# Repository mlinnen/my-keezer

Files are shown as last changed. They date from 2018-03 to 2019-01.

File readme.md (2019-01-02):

# Overview
This is my custom controller for my keezer.  I am building this from the ground up because I have some very specific ideas that I want to include and I have found no other solution (custom or off the self) that meets my needs.

## Build status
Master Branch  
Dev Branch 

## Goals 
I have a number of goals I want to achieve for this custom controller.  At this point I doubt all of this could or should be done on a single ESP8266 micro.  It is likely I will have a number of ESP8266's that work together over MQTT to achieve all of the functionality I want.  This project will evolve over a long period of time.

### Future list of features
Check out the [Github Issues (label enhancements)](https://github.com/mlinnen/my-keezer/labels/enhancement) for a list of features that are planned for a later date.

## Features
This is a list of actual features the current code base supports.

### Current list of features
* Measure the temperature inside the keezer with two temperature sensors (one at the top and one at the bottom).
* Measure the temperature outside the keezer.
* Control the keezer temperature given a temperature set point and the temperature sensor reading ().
* Display the current temperature of the keezer on an LCD.
* Turn on/off a fan(s) to circulate the air in the keezer when the difference between the top and bottom sensors is greater than a given threshold.  
* Detect motion when someone approaches the keezer.
* Turn on LED lighting and LCD display when someone approaches and turn off the lighting and LCD display after a delay.
* Connects to MQTT broker using a user name and password.
* Broadcast over MQTT sensor readings such as: temperature and motion.
* Broadcast over MQTT event changes such as: compressor, fan and lights turning on/off.
* Respond to an MQTT ping request so that an external application can determine what keezers are online.
* Allow the keezer to join a wifi network without changing the code
* Allow for the keezer to join a new Wifi or a different MQTT broker by holding down the mode pushbutton for > 3 seconds.
* The keezer continues to maintain the temperature of the beer even if the Wifi is down or the MQTT broker is down.  The highest priority is to keep the beer nice and cold.

## Hardware
* 3 DS18B20 Temperature Sensors
* 1 4.7K Resistor
* 1 [HUZZAH ESP8266](https://www.adafruit.com/product/2471)
* 1 [4 Channel Relay Board](https://www.sunfounder.com/4-channel-5v-relay-shield-module.html)
* 1 [4 x 20 LCD](https://www.adafruit.com/product/498)
* 1 [I2C / SPO character LCD backpack](https://www.adafruit.com/product/292)
* 1 [12v 5A switching power supply](https://www.adafruit.com/product/352)
* 1 [Mini DC/DC Converter 5v @ 1A](https://www.adafruit.com/product/1065)
* 1 [LED Strip Light Triangle Bulbs](https://www.amazon.com/Triangle-Bulbs-T93003-Waterproof-Flexible/dp/B00IZA2URS)

## Wiring
I used Fritzing to document the wiring of all components.  After installing Fritzing just open the doc\keezer.fzz file from Fritzing.  Or you can look at the doc\Wiring.png file.

## I/O
* 1 gpio for 1 wire for temperature sensors
* 1 gpio for relay dc fan
* 1 gpio for relay LED light strip
* 1 gpio for relay compressor
* 1 gpio for motion sensor
* 2 gpio for LCD
* 1 gpio for push button LCD mode

### LCD Display layout
A push button allows you to change the mode of the LCD.  Mode 1 is the default mode and after a certain amount of time the LCD will fall back into this mode.

Example Mode 1 Top, Average & Bottom Compressor on
```
Current Temperature
Set  43.0 Top 44.5
          Avg 43.5
Comp On   Bot 42.5
```  
Example Mode 1 Top, Average & Bottom Compressor off
```
Current Temperature
Set  43.0 Top 44.5
          Avg 43.5
Comp Off  Bot 42.5
```  

Example Mode 2 External Temperature
```
Current Temperature
          Ext 82.0
        
Comp Off          
```

Example Mode 3 Set Temperature
```
Set Temperature
High          44.0
Avg           43.0
Low           42.0
```

## Dependencies
This application depends on the following libraries:
* OneWire
* DallasTemperature
* RBD_Timer
* RBD_Button
* Adafruit LiquidCrystal
* PubSubClient
* WifiManager
* ArduinoJson

## Build
There are a couple things you need to do so that you can compile the project. I converted this project to use [Platform IO](https://platformio.org/) so you will need to install it as well as an editor. I personally think that the Visual Studio code editor works very well with Platform IO.

1. Make a copy of the myconfig.sample.h and rename it myconfig.h
2. Edit the myconfig.h and set the specific topics that you want the keezer to use (or leave them as is).  If you have more than 1 keezer make sure you changed the integer in all the topics so that one keezer can be addressed differently than the other keezer
3. You can also make changes to the default settings in myconfig.h
4. TODO Detail how someone sets the right index values for the temperature sensors since they are different for every sensor.
5. Place the ESP8266 into flash mode
6. Run the following command 
        pio run --target upload
7. The first time that the application is downloaded to the target platform it will put the device in an Access Point mode which will allow you to configure it for connection to your Wifi
8. Open your Wifi and connect to "mykeezer-ap". Note you have 120 seconds after power on to complete this task before the keezer falls out of AP mode and starts controlling the temperature of the beer.  If you dont complete this process before the 120 second timeout simply cycle the power on the keezer and try again
9. Click on the Wifi setup button and fill in the text fields.  Once the information is submitted the device will connect to Wifi and the MQTT broker
10. If you need to change the MQTT or Wifi settings just hold in the mode button for longer than 4 seconds and the device will become an Access Point again for configuration.

## MQTT
The only way to communicate with the keezer is to use MQTT messages.  Currently the integration is mostly one way (keezer publishing messages to MQTT), but at some point you will be able to control aspects of the keezer by sending messages to it.  If you have never used MQTT before then I would advise you to head on over to [MQTT.org](http://mqtt.org/) to learn more about it.

**Note:** This is a work in progress and I am likely going to re-factor these MQTT topics and message formats as I evolve the application over time.

## Topics and Messages
The Topics and Messages that the keezer uses will be defined here so that you have one place for determining how to interact with it.  You can also edit the mymqttbroker.h file to customize how you want your topics to be defined on the MQTT bus.  For instance not everyone will want their MQTT topics to start with /home/keezer like I have put together.  Hopefully this meets everyones needs on allowing the keezer to exist along with any other MQTT topics you have on your network.

### MQTT Subscriptions
The following subscriptions are supported by the keezer.

#### Keezer ping
This allows some external application to request what keezers are on the bus.  Each keezer (if you have multiple) will respond to this ping request.
``` 
/home/keezer/ping 
```

### MQTT Publications

#### Keezer ping response
In response to the ping request each keezer will publish the following.  Where {id} is the unique id (integer) of the keezer.  This allows for more than one keezer to exist on the bus.
``` 
/home/keezer/pingr/{id} 
```

#### Keezer temperatures
The keezer will broadcast the current temperature readings.  Where {id} is the unique id (integer) of the keezer.  The body of the message contains a floating point number that represents Fahrenheit.  There are multiple temperature readings that the keezer tracks: Average, Top and Bottom. 
``` 
/home/keezer/{id}/temp/avg {float}
/home/keezer/{id}/temp/top {float}
/home/keezer/{id}/temp/bottom {float}
```

#### Keezer motion detection
The keezer will broadcast the status of the motion detector when it changes.  Where {id} is the unique id (integer) of the keezer.  The body of the message contains a 1 or 0 indicating if there was motion detected (1) or motion has stopped being detected (0). 
``` 
/home/keezer/{id}/motion/value 1
/home/keezer/{id}/motion/value 0
```

#### Keezer compressor status
The keezer will broadcast when the compressor is turned on/off.  Where {id} is the unique id (integer) of the keezer.  The body of the message contains a 1 or 0 indicating if the compressor was turned on (1) or off (0).
``` 
/home/keezer/{id}/compressor/value 1
/home/keezer/{id}/compressor/value 0
```

#### Keezer fan status
The keezer will broadcast when the fan(s) is turned on/off.  Where {id} is the unique id (integer) of the keezer.  The body of the message contains a 1 or 0 indicating if the fan was turned on (1) or off (0).
``` 
/home/keezer/{id}/fan/value 1
/home/keezer/{id}/fan/value 0
```

#### Keezer light status
The keezer will broadcast when the light is turned on/off.  Where {id} is the unique id (integer) of the keezer.  The body of the message contains a 1 or 0 indicating if the light was turned on (1) or off (0).
``` 
/home/keezer/{id}/light/value 1
/home/keezer/{id}/light/value 0
```

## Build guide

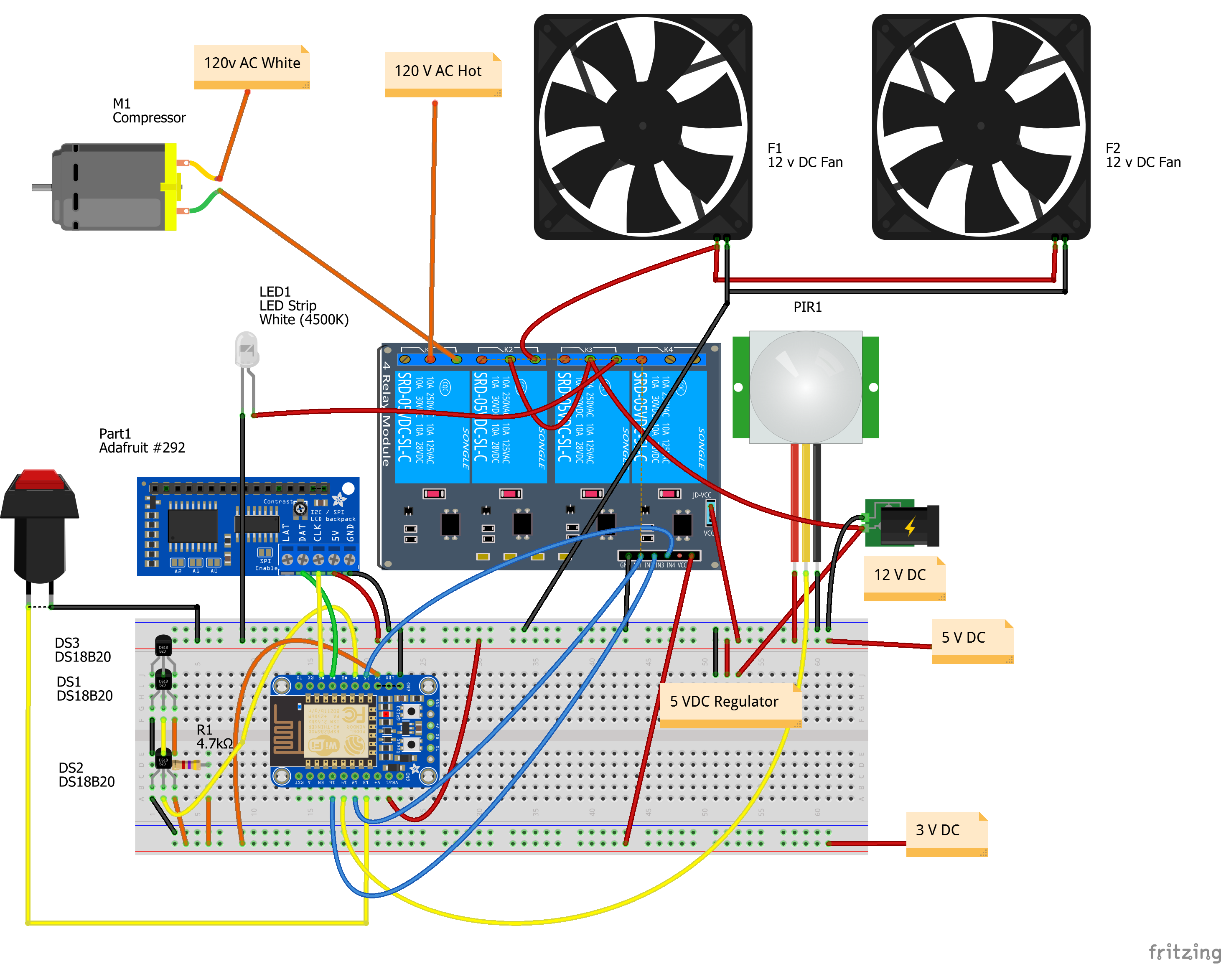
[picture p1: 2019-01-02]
doc/Wiring.png

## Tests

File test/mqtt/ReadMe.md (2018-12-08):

This contains some windows batch files to send out MQTT messages to the keezer for testing purposes.  Since the MQTT broker needs a user name password you will need to copy the config.sample.ini to config.ini and edit the file with the IP, user name and password for the broker.  This keeps the secrets out of source control.

These test tools are dependent on python and paho-mqtt, so make sure you have python installed and also install paho-mqtt with the following command:
```
pip install paho-mqtt
```

monitor.py will monitor a topic in a continuous loop and output the topic and payload to the console when one is received. You can call this python script from a windows command line as follows:
```
python monitor.py -c "config.ini" -t /home/#
```

publish.py will publish a given message on the given topic. You can call this python script from a windows command line as follows:
```
python publish.py -c "config.ini" -t /home/keezer/ping -m " "
```

monitor.bat is an example windows batch file that calls the monitor.py passing in some valid parameters.

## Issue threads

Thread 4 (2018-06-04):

Broadcast current temperature readings over MQTT

mlinnen, 2018-06-04:
The following temperatures should be broadcasted over MQTT:
Lower Temperature Sensor
Upper Temperature Sensor
Average Temperature Sensor

The program should still be able to control the temperature of the keezer even if the Wifi is down or MQTT broker is down.

Closed 2018-12-09.

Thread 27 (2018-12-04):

Convert project over to platform io

mlinnen, 2018-12-04:
The platform io framework creates a better structure for multiple platforms, library management and unit testing.

mlinnen, 2018-12-08:
Resolved by PR #29

Closed 2018-12-08.

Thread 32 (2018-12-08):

Add the ability to join the Wifi network without changing the code and re-uploading a new version to the microcontroller

mlinnen, 2018-12-08:
The process for joining a network cannot interfere with the ability of the keezer to stay at the programmed temperature.

Closed 2018-12-31.

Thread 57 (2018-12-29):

Simplify how to change Wifi and MQTT Broker settings

mlinnen, 2018-12-29:
It is currently difficult to change the Wifi settings or the MQTT broker settings once they are set.  There needs to be a way to place the device into AP mode and prompt for the settings again so that you can change them when you need to without re-uploading code to achieve the same thing.

Closed 2018-12-31.

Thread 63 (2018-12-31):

Enters Wifi AP mode when it shouldn't

mlinnen, 2018-12-31:
**Describe the bug**
When powering up the device enters Wifi AP mode even though the Wifi has been configured.  Even setting the Wifi configuration again causes the device to enter Wifi AP Mode again. The only way to get past this step is to wait for the 2 minute timeout and then the keezer works as expected (even connected to wifi)

**To Reproduce**
Steps to reproduce the behavior:
1. Download the Dev branch code and upload into the device
2. Plug the ESP8266 into the keezer and power it up
3. The LCD display states that the keezer is in AP Mode.
4. Go ahead and connect to mykeezer-ap and configure the wifi access
5. After submitting the wifi config page the LCD is still noting that the keezer is in AP Mode.

**Expected behavior**
If the Wifi is configured correctly on bootup the LCD should never display AP mode.  The keezer should connect to the Wifi and just start working.

**Additional context**
This doesn't seem to happen if the ESP8266 is on a breadboard and connected to just a mode button switch.

Closed 2018-12-31.

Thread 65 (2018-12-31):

State is not always broadcasted over MQTT on boot up

mlinnen, 2018-12-31:
**Describe the bug**
When the keezer is turned on the initial state is not broadcasted over MQTT on the first time through the loop

**To Reproduce**
Steps to reproduce the behavior:
1. Make sure you are monitoring the keezer via MQTT
2. Power up the keezer but make sure you are not in range of the motion sensor
3. Notice that the state of the following is not broadcasted over MQTT: lights, motion, fan or compressor

**Expected behavior**
The state of these items is broadcasted when the loop is executed the first time after power up

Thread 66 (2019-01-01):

MQTT Saved settings are deleted on power outage

mlinnen, 2019-01-01:
**Describe the bug**
The MQTT settings are cleared out after the power is cycled on the keezer

**To Reproduce**
Steps to reproduce the behavior:
1. Power up the keezer and wait for it to boot
2. Open up an MQTT monitor to watch for any temp values coming from the keezer
3. Notice that no temp values are coming from the keezer and it also does not respond to a MQTT ping request.

**Expected behavior**
After powering the keezer off and then back on the MQTT settings are pulled from the config file and used to connect to MQTT bus

Closed 2019-01-02.

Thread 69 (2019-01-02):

LCD Display corrupted when entering mode 0 for Wifi setup

mlinnen, 2019-01-02:
**Describe the bug**
The LCD Display is not cleared and displays some incorrect data when in Mode 0 for Wifi connection changes

**To Reproduce**
Steps to reproduce the behavior:
1. Hold down the mode switch for > 5 seconds
2. The LCD attempts to display the Wifi connection message but also has some left over temp readings mixed in

**Expected behavior**
The LCD should be cleared between mode switching

Closed 2019-01-02.

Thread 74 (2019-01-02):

Display the status of the Fans on the LCD

mlinnen, 2019-01-02:
**Is your feature request related to a problem? Please describe.**
No

**Describe the solution you'd like**
The LCD display already shows when the compressor is on or off.  The fan should also be displayed on the LCD when it is on or off.

**Describe alternatives you've considered**
None

**Additional context**

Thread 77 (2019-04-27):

Loses connection to MQTT broker

mlinnen, 2019-04-27:
If the wifi goes down like in a power outage scenario and the keezer comes up before the wifi does then all MQTT updates stop working unless you cycle the power on the keezer after the wifi is back up.

**To Reproduce**
Steps to reproduce the behavior:
1. Turn off wifi
2. Cycle the power on the keezer
3. After the keezer is up and running (LCD Display is showing the temperature) turn on the wifi
4. Wait for the wifi to become active then check if the temperature readings are being broadcast to the broker

**Expected behavior**
A clear and concise description of what you expected to happen.

**Screenshots**
If applicable, add screenshots to help explain your problem.

**Additional context**
Add any other context about the problem here.

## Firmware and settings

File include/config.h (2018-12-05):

/************************* Temperature Controller *********************************/

#define DEFAULT_TEMPERATURE_SETPOINT_HIGH 40.0
#define DEFAULT_TEMPERATURE_SETPOINT_LOW  38.0

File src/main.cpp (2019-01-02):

#include "main.h"

void setup()
{
  Serial.begin(9600);

  randomSeed(micros());

  keezerlcd_setup();

  // Delay a little bit to give a developer time to connect the monitor to the serial port before running through the rest os the setup
  delay(5000);

 if (SPIFFS.begin()) {
    Serial.println("mounted file system");
    
    jsonfile_load("/config.txt",config);
    jsonfile_print("/config.txt");

    keezerwifi_setup(config, false);

    if (keezerwifi_saveConfig()) {
      Serial.println("Going to save config");
      jsonfile_save("/config.txt", config);
      jsonfile_print("/config.txt");
    }

    mqtt_setup(config);

  } else {
    Serial.println("failed to mount FS");
  }

  // Run the setup on the temparature controller
  temperaturecontroller_setup(config.temperature_set_point_low,config.temperature_set_point_high,config.publish_temperature_seconds);
  
  // Run the setup on the light controller
  lightcontroller_setup(config.motion_timeout_seconds,config.light_on_seconds);
  
}

void loop()
{
  // Connect to Wifi if not connected
  keezerwifi_loop(config);

  if (keezerwifi_saveConfig()==true) {
      jsonfile_save("/config.txt", config);
      jsonfile_print("/config.txt");
  }

  // Process all the loops
  mqtt_loop(config);

  temperaturecontroller_loop(config.temperature_fan_set_point_low,config.temperature_fan_set_point_high);

  lightcontroller_loop();

  mqtt_publish();

  // TODO Determine if any state changes or sensor changes need to be broadcasted out over MQTT
}

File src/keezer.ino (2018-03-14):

#include "TemperatureController.h"
#include "LightController.h"
#include "TemperatureLCD.h"
#include "ctype.h"
#include "config.h"

TemperatureController *tempController;
LightController *lightController;

void setup()
{
  Serial.begin(9600);

  // Delay a little bit so we can catch the serial port data during setup
  delay(5000);

  tempController = new TemperatureController(
    16, 12, 
    DEFAULT_TEMPERATURE_SETPOINT_LOW, 
    DEFAULT_TEMPERATURE_SETPOINT_HIGH);
  lightController = new LightController(14,15);

  tempController->setup();
  lightController->setup();
}

void loop()
{
  // TODO Look for any messages that came in over MQTT

  // Process all the loops
  tempController->loop();
  lightController->loop();

  // TODO Determine if any state changes or sensor changes need to be broadcasted out over MQTT
}

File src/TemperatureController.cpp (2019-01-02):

#include "temperatureController.h"

#define COMPRESSOR_RELAY_PIN 12
#define FAN_RELAY_PIN 16
#define MODE_BUTTON_PIN 13

RBD::Button _modeButton(MODE_BUTTON_PIN);

int _mode=-1;
boolean _compressor = false;
boolean _lastCompressor;
boolean _waitforButtonRelease = false;
boolean _fan = false;
boolean _lastFan;
float _lowSetpoint = 0;
float _highSetpoint = 0;
boolean _publishTemperature = false;
boolean _publishCompressor = false;
boolean _publishFan = false;
RBD::Timer _publishTempTimer;
void publish(const char* topic, float temp);
void publish(const char* topic, boolean compressor);
unsigned long pressedTime;

void temperaturecontroller_setup(float lowSetpoint, float highSetpoint, int publishTemperatureSeconds)
{
  _lowSetpoint = lowSetpoint;
  _highSetpoint = highSetpoint;

  // Perform any onetime setup.
  temperaturesensor_setup(false,1);

  _publishTempTimer.setTimeout(publishTemperatureSeconds * 1000);
  _publishTempTimer.restart();

  pinMode(COMPRESSOR_RELAY_PIN, OUTPUT);
  pinMode(FAN_RELAY_PIN, OUTPUT);
  digitalWrite(FAN_RELAY_PIN, HIGH);
  digitalWrite(COMPRESSOR_RELAY_PIN, HIGH);
  
}

boolean temperaturecontroller_compressor()
{
  return _compressor;
}

float temperaturecontroller_averageSetPointTemperature()
{
  return (_lowSetpoint + _highSetpoint)/2;
}

float temperaturecontroller_lowSetPointTemperature()
{
  return _lowSetpoint;
}

float temperaturecontroller_highSetPointTemperature()
{
  return _highSetpoint;
}

boolean temperaturecontroller_loop(float fanTemperatureLow, float fanTemperatureHigh)
{
  boolean refreshLCD = false;

  // Capture when the mode button was first pressed
  if (_modeButton.onPressed())
  {
    pressedTime = millis();
    _waitforButtonRelease = true;
  }
  if (_modeButton.onReleased() && _waitforButtonRelease)
  {
    unsigned long releaseTime;
    releaseTime = millis();
    _waitforButtonRelease = false;
    // Determine if the mode button was pressed for a long time (>3 seconds)
    if ((releaseTime-pressedTime)/1000 > 3) {
      Serial.println("Mode button released long press");
      temperaturecontroller_changeMode(0);
    }
    else
    {
      Serial.println("Mode button released short press");
      temperaturecontroller_changeMode();
      refreshLCD = true;
    }
  }

  // Check if a new set of temp readings exist
  if (temperaturesensor_loop() == true)
  {

    if (temperaturesensor_averageTemperature()<_lowSetpoint) {
      _compressor = false;
      digitalWrite(COMPRESSOR_RELAY_PIN,HIGH);
    }
    if (temperaturesensor_averageTemperature()>_highSetpoint) {
      _compressor = true;
      digitalWrite(COMPRESSOR_RELAY_PIN,LOW);
    }

    // Look at the difference between the top and bottom temperature sensor to determine when the fans should be on
    float tempDelta = abs(temperaturesensor_topTemperature() - temperaturesensor_bottomTemperature());
    if (tempDelta>fanTemperatureHigh) { 
      _fan = true; 
      digitalWrite(FAN_RELAY_PIN,LOW);
    }
    if (tempDelta<fanTemperatureLow) { 
      _fan=false; 
      digitalWrite(FAN_RELAY_PIN,HIGH);
    }

    if (_compressor != _lastCompressor)
    {
      _publishCompressor = true;
      if (_compressor) {Serial.println("Compressor On");}
      else {Serial.println("Compressor Off");}
    }
    _lastCompressor = _compressor;

    if (_fan != _lastFan)
    {
      _publishFan = true;
      if (_fan) {Serial.println("Fan On");}
      else {Serial.println("Fan Off");}
    }
    _lastFan = _fan;

    refreshLCD = true;
  }
  
  // if the keezer lights are on then turn on the LCD
  if (lightcontroller_light()) {
    keezerlcd_on();
  }
  else {
    keezerlcd_off();
  }

  if (_publishTempTimer.isExpired())
  {
    _publishTemperature = true;
    Serial.print("Hi  Setpoint ");
    Serial.println(temperaturecontroller_highSetPointTemperature(), 1);
    Serial.print("Avg Setpoint ");
    Serial.println(temperaturecontroller_averageSetPointTemperature(), 1);
    Serial.print("Low Setpoint ");
    Serial.println(temperaturecontroller_lowSetPointTemperature(), 1);

    Serial.print("Avg Temp ");
    Serial.print(temperaturesensor_averageTemperature(), 1);
    Serial.println();
    Serial.print("Bot Temp ");
    Serial.print(temperaturesensor_bottomTemperature(), 1);
    Serial.println();
    Serial.print("Top Temp ");
    Serial.print(temperaturesensor_topTemperature(), 1);
    Serial.println();
    Serial.print("Ext Temp ");
    Serial.print(temperaturesensor_exteriorTemperature(), 1);
    Serial.println();

    _publishTempTimer.restart();
  }

  if (refreshLCD) {keezerlcd_print();}

  return true;
}

void temperaturecontroller_publish(PubSubClient &mqttClient) {

  if (_publishCompressor) {
    temperaturecontroller_publish(mqttClient, MQTT_TOPIC_COMPRESSOR, _compressor);
    _publishCompressor = false;
  }

  if (_publishFan) {
    temperaturecontroller_publish(mqttClient, MQTT_TOPIC_FAN, _fan);
    _publishFan = false;
  }

  if (_publishTemperature) {
    temperaturecontroller_publish(mqttClient, MQTT_TOPIC_TEMP_AVG, temperaturesensor_averageTemperature());
    temperaturecontroller_publish(mqttClient, MQTT_TOPIC_TEMP_BOTTOM, temperaturesensor_bottomTemperature());
    temperaturecontroller_publish(mqttClient, MQTT_TOPIC_TEMP_TOP, temperaturesensor_topTemperature());
    temperaturecontroller_publish(mqttClient, MQTT_TOPIC_TEMP_EXTERIOR, temperaturesensor_exteriorTemperature());
    _publishTemperature = false;
  }
}

void temperaturecontroller_publish(PubSubClient &mqttClient, const char* topic, float temp)
{
    if (mqttClient.connected()) 
    {
      String temp_str; 
      char message_buff[20];
      temp_str = String(temp);
      temp_str.toCharArray(message_buff, temp_str.length() + 1); 
      mqttClient.publish(topic, message_buff, true);
    }
}

void temperaturecontroller_publish(PubSubClient &mqttClient, const char* topic, boolean value)
{
    if (mqttClient.connected()) 
    {
      if (value) {
        mqttClient.publish(topic, "1", true);
      }
      else {
        mqttClient.publish(topic, "0", true);
      }
    }
}

int temperaturecontroller_mode()
{
  return _mode;
}

void temperaturecontroller_changeMode()
{
  _mode = _mode + 1;
  if (_mode>3) {_mode = 1;}
  Serial.print("Mode: ");
  Serial.println(_mode);
}

void temperaturecontroller_changeMode(int mode)
{
  _mode = mode;
  Serial.print("Mode: ");
  Serial.println(_mode);
}

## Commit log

2018-02-23 Temperature readings
2018-02-27 Added output to control relay
2018-02-27 First set of features to control a keezer (#1)
    * Temperature readings
    * added build file
    * Updated libraries for travis build
    * updated build definition
    * More build changes
    * Added another dependency
    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
2018-03-06 When printing the temp only show one decimal place
2018-03-07 fixed a build issue
    [config.sample.h]
2018-03-08 Refresh the LCD if the mode changes or we read the temperature
2018-03-11 Added Fan control, motion detect and light control
2018-03-12 Switched top and bottom temp sensors
2018-03-12 Wiring documentation
    [keezer.fzz]
2018-03-12 Some additional documentation on wiring
2018-03-13 Updated fritzing doc
    [keezer.fzz]
2018-03-13 Fixed some bugs with the LCD display
    [TemperatureController.ino]
2018-04-30 Corrected relay polarity
2018-04-30 Corrected Wiring diagram
    [keezer.fzz]
2018-05-12 Bug where lights would not turn off after the 2 min timer should have expired
2018-12-07 Fixed some compiler warnings
    [LightController.cpp, TemperatureController.cpp, TemperatureSensor.cpp]
2018-12-07 copy the config.sample.h to config.h
2018-12-08 Convert to Platform IO (#29)
    * First set of features to control a keezer (#1)
    * changes
    * Show build status, put average calc in TempSensor
    * Pulled 2 features off the list since they were not complete yet
    * Label the build icons
    * Readme formatting
    * Added output to control relay
    * Updated the readme
    * Corrected relay polarity
    * Corrected Wiring diagram
    * Bug where lights would not turn off after the 2 min timer should have expired
    * #6 updated the documentation
    * #6 updated the documen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
    [LightController.cpp, TemperatureController.cpp, TemperatureSensor.cpp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]
2018-12-08 Make a copy of the mywifi.sample.h file so that travis ci can compile the application
2018-12-08 Placed the Ping and Pingr MQTT topics into the broker config header so that it can be changed without commiting these changes to the main source
    [main.cpp]
2018-12-08 Publish the temperature readings to MQTT
2018-12-08 Make sure we can control the temp of the keezer even when we are not connected to wifi or mqtt broker
    [main.cpp]
2018-12-08 Mqtt temp (#34)
    Mqtt temperature and ping
2018-12-09 Publish fan status on MQTT
2018-12-09 Fan topic
2018-12-09 Revert "Merge pull request #39 from mlinnen/PublishFan"
    This reverts commit 20fa4309246e79c77318d58b1d322eed9db564b9, reversing
    changes made to a5ecf80444290dd5e0414801257d7a05425ec6dc.
    [LightController.cpp, TemperatureController.cpp, config.sample.h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]
2018-12-15 Convert timer value to milliseconds
2018-12-15 Turn on/off fan(s) based on the difference between the bottom and top temperature sensor
2018-12-15 Updated the current features list
2018-12-17 Fan bug
2018-12-17 Fixed bug with fan control
    [TemperatureController.cpp]
2018-12-18 Refactored sending serial output and compressor/fan control
2018-12-23 Fixed a wiring error
    [keezer.fzz]
2018-12-23 Wiring error
2018-12-23 Bug with retrieving the temp sensor values
    [TemperatureController.cpp]
2018-12-23 Fixed some config settings
    [config.sample.h]
2018-12-26 Updated to install ArduinoJson and WifiManager for the build
2018-12-28 renamed the wifi files to avoid conflicts
    [keezzerwifi.cpp, main.cpp]
2018-12-29 case sensitive include
2018-12-29 case sensitivity change
2018-12-29 v=case sensitivity change
2018-12-31 Allow for the Wifi and MQTT to be reconfigured by holding down the mode button for more than 3 seconds
2018-12-31 Updated the wiring diagram to include the mode switch
    [keezer.fzz]
2019-01-01 Added a 3rd temp sensor for measuring temp outside the keezer
    [keezer.fzz]
2019-01-01 Corrected the index for the onewire temp sensors
    [TemperatureSensor.cpp]
2019-01-02 Fixed a bug where MQTT settings were not saved after manual wifi setup
    [keezzerwifi.cpp, main.cpp]
2019-01-02 #69 Clear the display when switching modes
2019-01-02 Dosumentation updates
    [keezer.fzz]
